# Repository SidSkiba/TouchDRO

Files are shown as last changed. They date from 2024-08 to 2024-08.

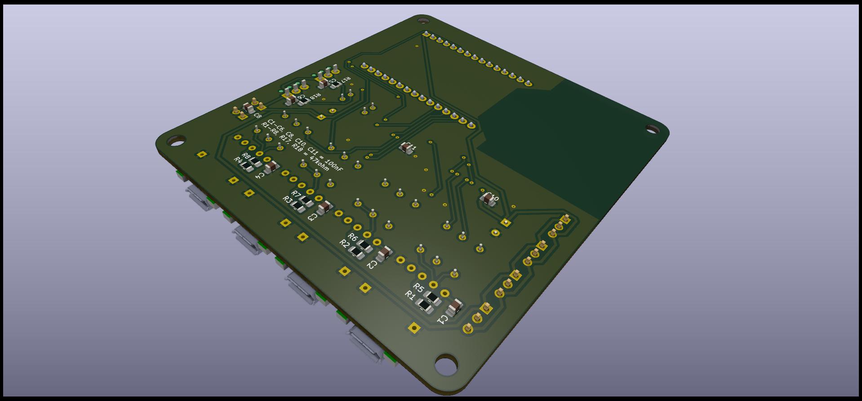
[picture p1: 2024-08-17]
Pictures/TouchDRO 6.jpg

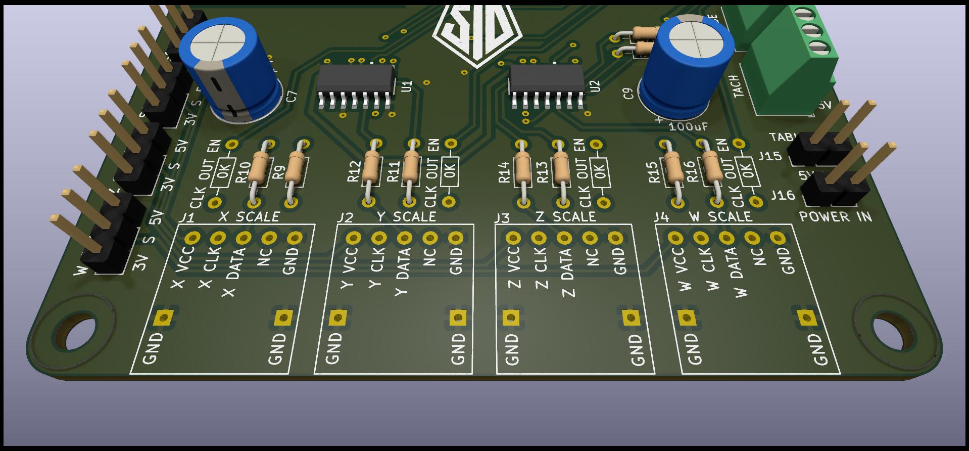
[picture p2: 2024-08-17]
Pictures/TouchDRO 10.jpg

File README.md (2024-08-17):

# TouchDRO
TocuhDRO PCB Kicad Design

PCB Design Files for a DIY TouchDRO PCB. This is based on information provided by https://www.touchdro.com/

All design done in Kicad 8.

Firmware files provided by https://www.touchdro.com/

All Gerber files included for JLCPCB to manufacture the circuit boards.

Design uses some surface mount components (some 0805 sized resistors and capacitors and sirface mount IC's) so you need to be comfortable with soldering those devices to the board.

Note that ESP32 module needs to be spaced 5mm above the circuit board.

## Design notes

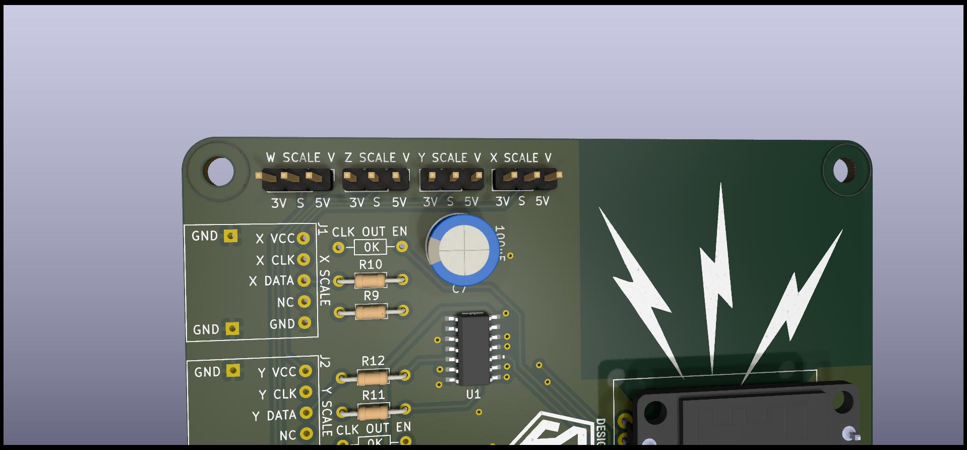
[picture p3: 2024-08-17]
Pictures/TouchDRO 11.jpg

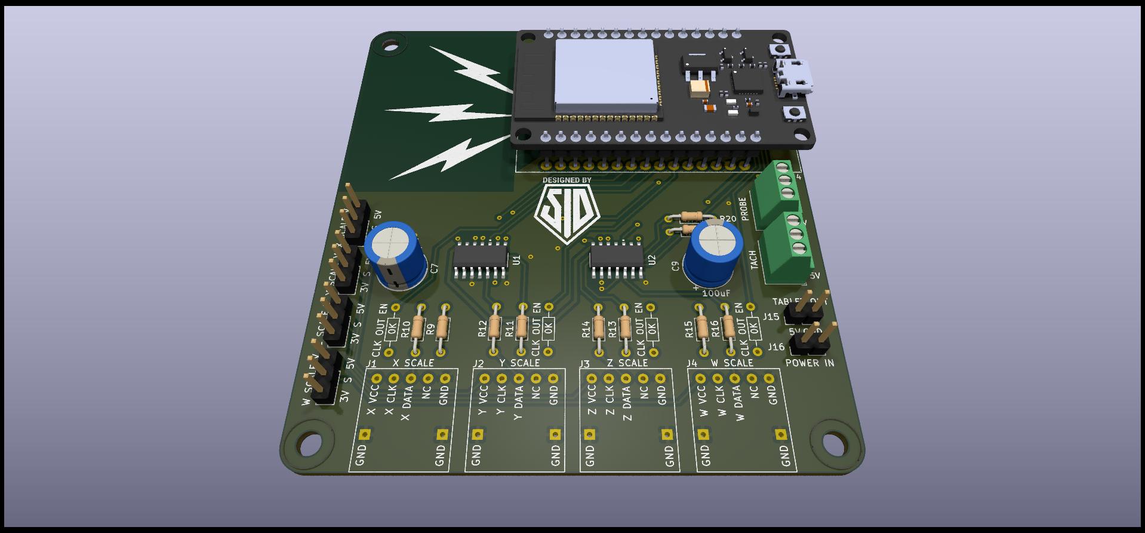
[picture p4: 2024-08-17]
Pictures/TouchDRO 9.jpg

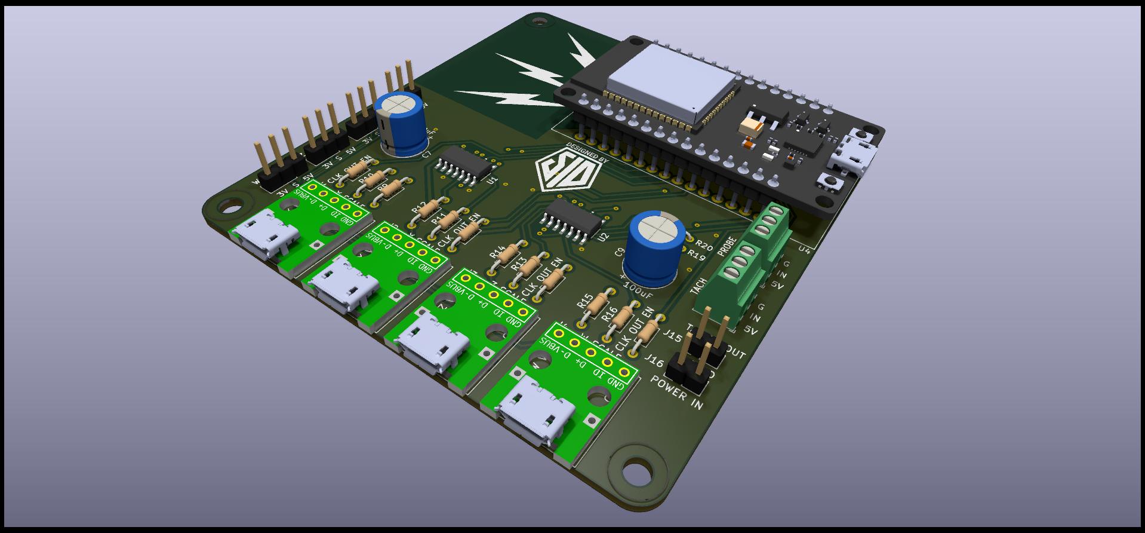
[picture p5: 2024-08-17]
Pictures/TouchDRO 4.jpg

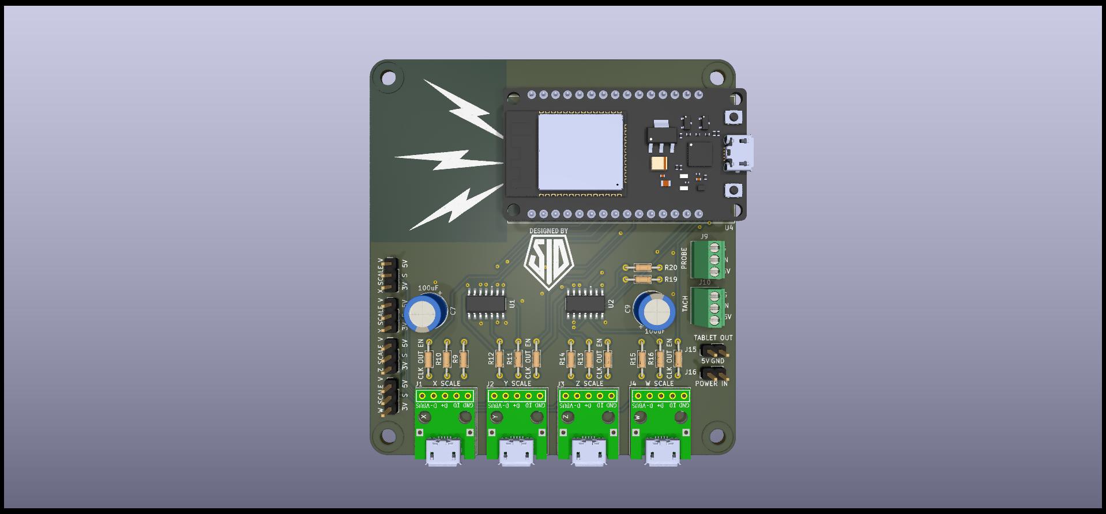
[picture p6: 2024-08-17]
Pictures/TouchDRO 2.jpg

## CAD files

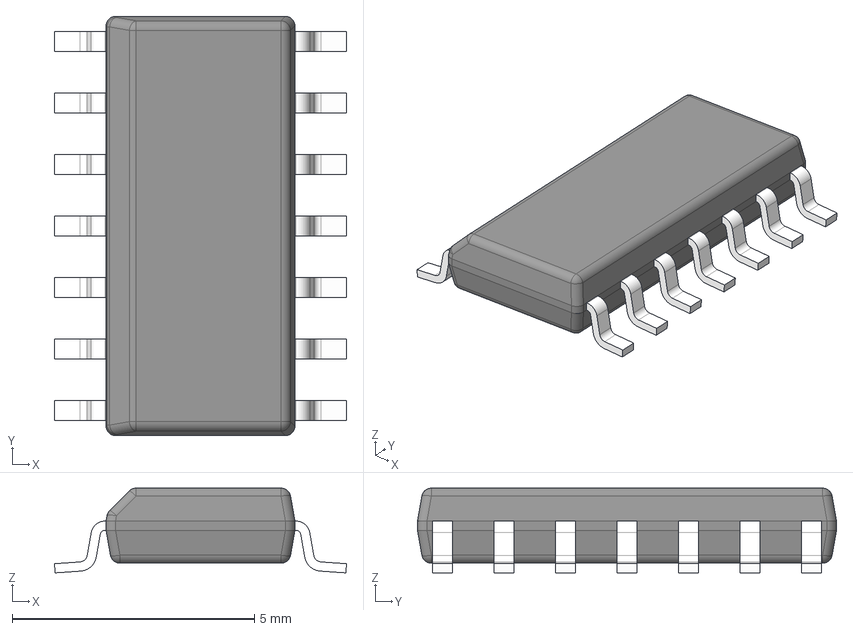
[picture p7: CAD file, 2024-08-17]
3D Models/CD74HC14M96.stp
6.03 x 8.65 x 1.75 mm
BODY-SO
LEAD-SO x 14
PIN1-ID

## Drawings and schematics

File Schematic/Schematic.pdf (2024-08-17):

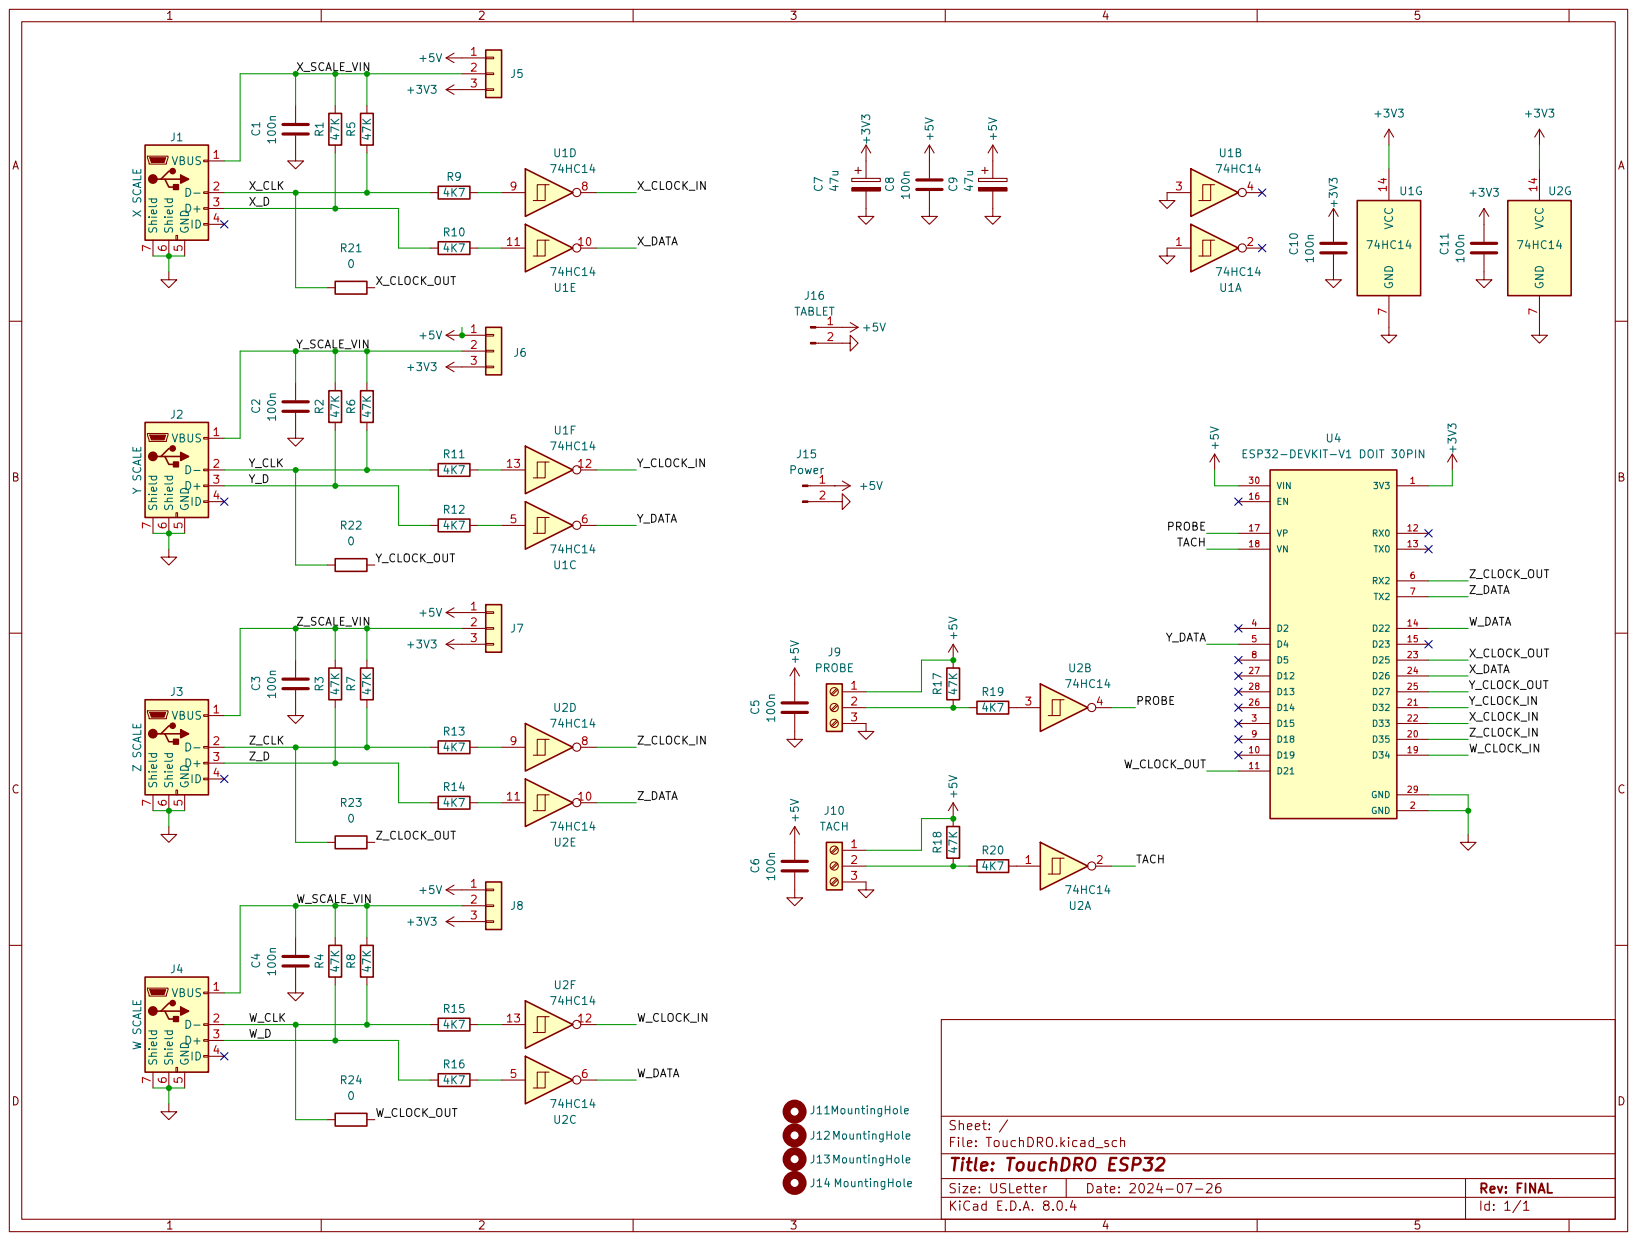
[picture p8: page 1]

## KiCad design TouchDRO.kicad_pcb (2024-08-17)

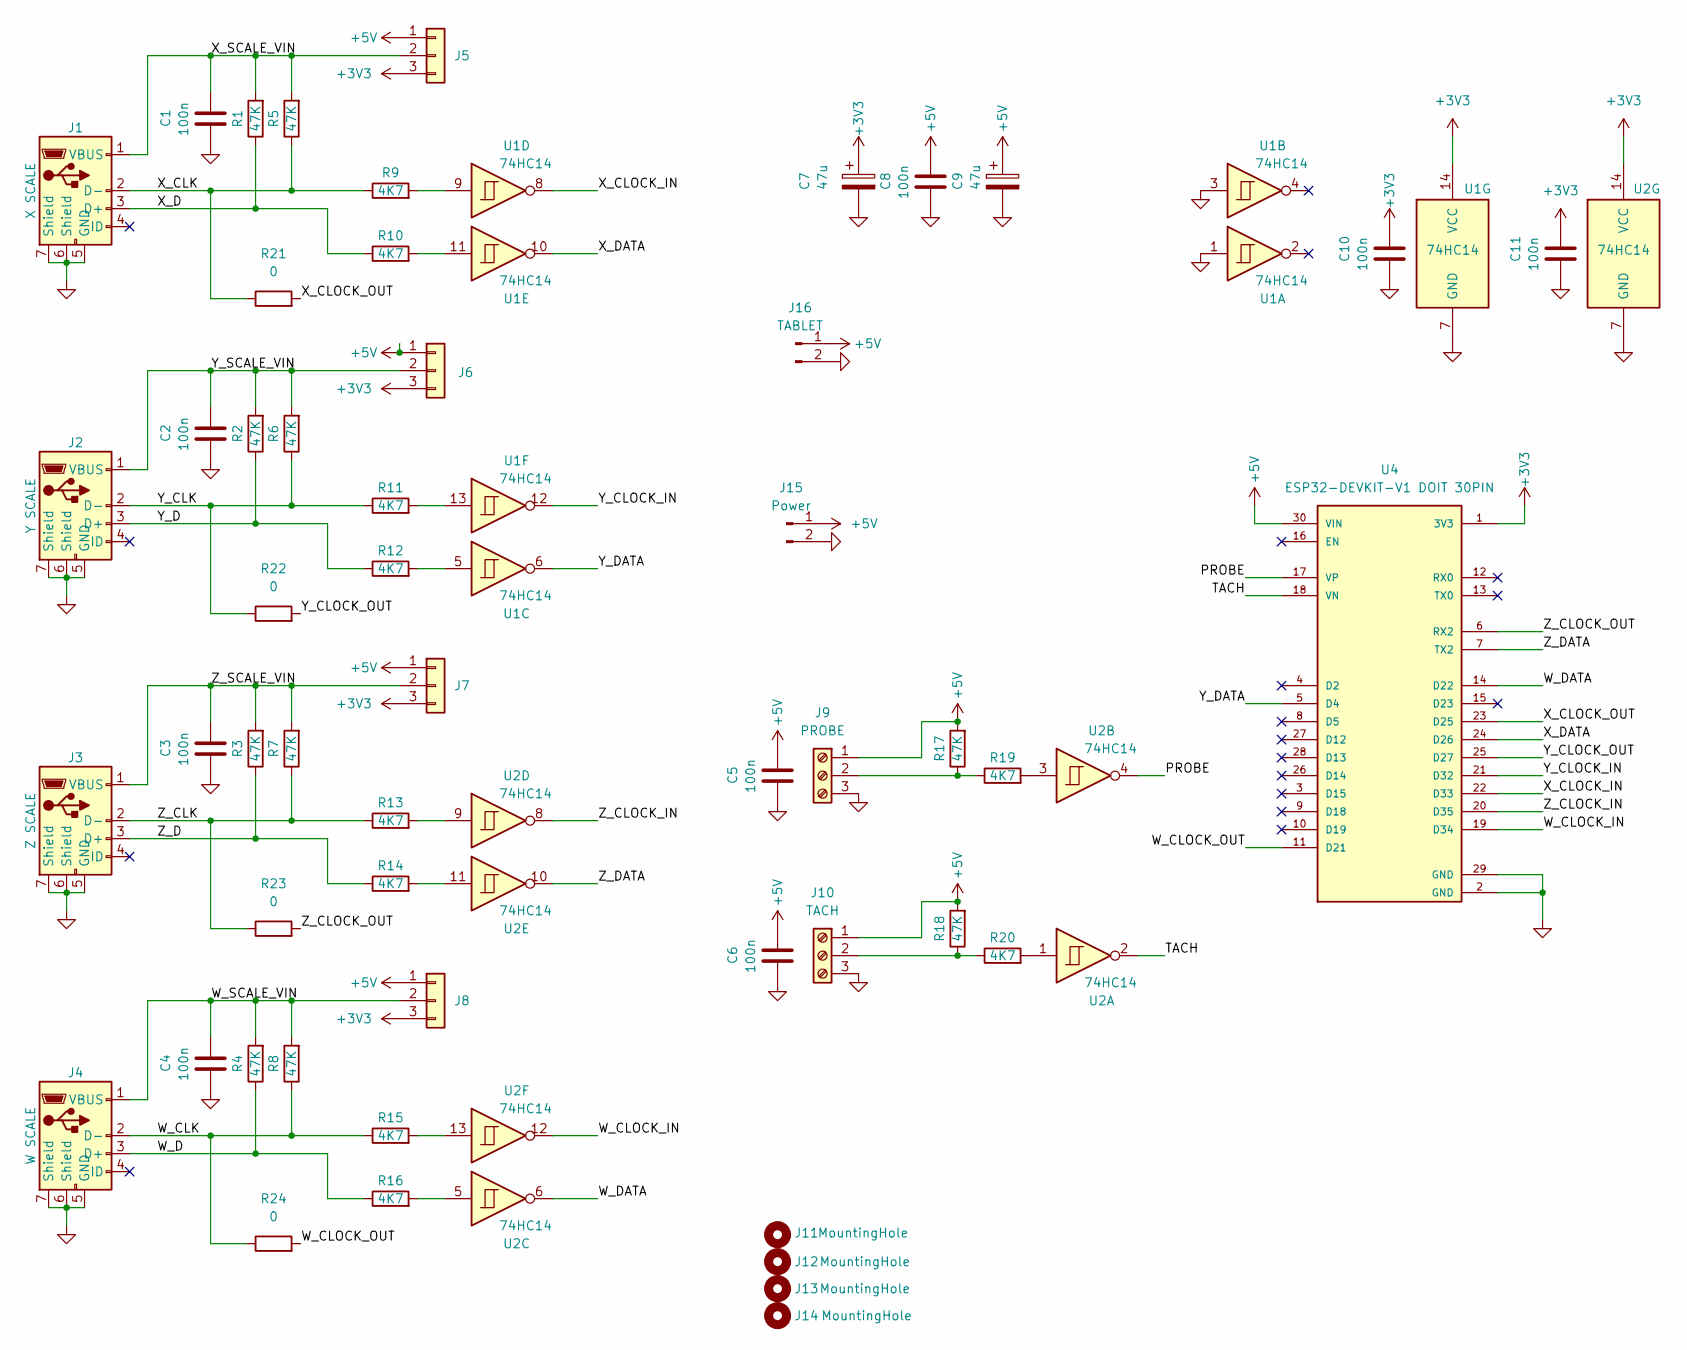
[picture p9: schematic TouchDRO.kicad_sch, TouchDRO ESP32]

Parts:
C1, C2, C3, C4, C5, C6, C8, C10, C11: 100n; C_0805_2012Metric_Pad1.18x1.45mm_HandSolder; LCSC C3034534
C7, C9: 47u; CP_Radial_D8.0mm_P3.50mm; LCSC 03EC0571
J1: X SCALE; USB Breakout Board
J2: Y SCALE; USB Breakout Board
J3: Z SCALE; USB Breakout Board
J4: W SCALE; USB Breakout Board
J5: X SCALE; PinHeader_1x03_P2.54mm_Vertical
J6: Y SCALE; PinHeader_1x03_P2.54mm_Vertical
J7: Z SCALE; PinHeader_1x03_P2.54mm_Vertical
J8: W SCALE; PinHeader_1x03_P2.54mm_Vertical
J9: PROBE; TerminalBlock_Phoenix_MPT-0,5-3-2.54_1x03_P2.54mm_Horizontal
J10: TACH; TerminalBlock_Phoenix_MPT-0,5-3-2.54_1x03_P2.54mm_Horizontal
J11, J12, J13, J14: MountingHole; MountingHole_3.5mm
J15: Power; PinHeader_1x02_P2.54mm_Vertical
J16: TABLET; PinHeader_1x02_P2.54mm_Vertical
R1, R2, R3, R4, R5, R6, R7, R8, R17, R18: 47K; R_0805_2012Metric_Pad1.20x1.40mm_HandSolder; LCSC C410613
R9, R10, R11, R12, R13, R14, R15, R16, R19, R20: 4K7; R_Axial_DIN0204_L3.6mm_D1.6mm_P7.62mm_Horizontal; LCSC C119339
R21, R22, R23, R24: 0; R_Axial_DIN0204_L3.6mm_D1.6mm_P7.62mm_Horizontal
U1, U2: 74HC14; 14PIN_SOIC; LCSC C2907
U4: ESP32-DEVKIT-V1 DOIT 30PIN; MODULE_ESP32_DEVKIT_V1 DOIT 30PIN; PARTREV N/A

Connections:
+3V3: C7.1, C10.1, C11.1, J5.3, J6.3, J7.3, J8.3, U1.14 (VCC), U2.14 (VCC), U4.1 (3V3)
+5V: C5.1, C6.1, C8.1, C9.1, J5.1, J6.1, J7.1, J8.1, J9.1, J10.1, J15.1, J16.1, R17.2, R18.2, U4.30 (VIN)
/PROBE: U2.4, U4.17 (VP)
/TACH: U2.2, U4.18 (VN)
/W_CLK: J4.2 (D-), R8.1, R15.1, R24.1
/W_CLOCK_IN: U2.12, U4.19 (D34)
/W_CLOCK_OUT: R24.2, U4.11 (D21)
/W_D: J4.3 (D+), R4.1, R16.1
/W_DATA: U2.6, U4.14 (D22)
/W_SCALE_VIN: C4.1, J4.1 (VBUS), J8.2, R4.2, R8.2
/X_CLK: J1.2 (D-), R5.1, R9.1, R21.1
/X_CLOCK_IN: U1.8, U4.22 (D33)
/X_CLOCK_OUT: R21.2, U4.23 (D25)
/X_D: J1.3 (D+), R1.1, R10.1
/X_DATA: U1.10, U4.24 (D26)
/X_SCALE_VIN: C1.1, J1.1 (VBUS), J5.2, R1.2, R5.2
/Y_CLK: J2.2 (D-), R6.1, R11.1, R22.1
/Y_CLOCK_IN: U1.12, U4.21 (D32)
/Y_CLOCK_OUT: R22.2, U4.25 (D27)
/Y_D: J2.3 (D+), R2.1, R12.1
/Y_DATA: U1.6, U4.5 (D4)
/Y_SCALE_VIN: C2.1, J2.1 (VBUS), J6.2, R2.2, R6.2
/Z_CLK: J3.2 (D-), R7.1, R13.1, R23.1
/Z_CLOCK_IN: U2.8, U4.20 (D35)
/Z_CLOCK_OUT: R23.2, U4.6 (RX2)
/Z_D: J3.3 (D+), R3.1, R14.1
/Z_DATA: U2.10, U4.7 (TX2)
/Z_SCALE_VIN: C3.1, J3.1 (VBUS), J7.2, R3.2, R7.2
GND: C1.2, C2.2, C3.2, C4.2, C5.2, C6.2, C7.2, C8.2, C9.2, C10.2, C11.2, J1.5 (GND), J1.6 (Shield), J1.7 (Shield), J2.5 (GND), J2.6 (Shield), J2.7 (Shield), J3.5 (GND), J3.6 (Shield), J3.7 (Shield), J4.5 (GND), J4.6 (Shield), J4.7 (Shield), J9.3, J10.3, J15.2, J16.2, U1.1, U1.3, U1.7 (GND), U2.7 (GND), U4.2 (GND), U4.29 (GND)
unnamed: J9.2, R17.1, R19.1
unnamed: J10.2, R18.1, R20.1
unnamed: R9.2, U1.9
unnamed: R10.2, U1.11
unnamed: R11.2, U1.13
unnamed: R12.2, U1.5
unnamed: R13.2, U2.9
unnamed: R14.2, U2.11
unnamed: R15.2, U2.13
unnamed: R16.2, U2.5
unnamed: R19.2, U2.3
unnamed: R20.2, U2.1

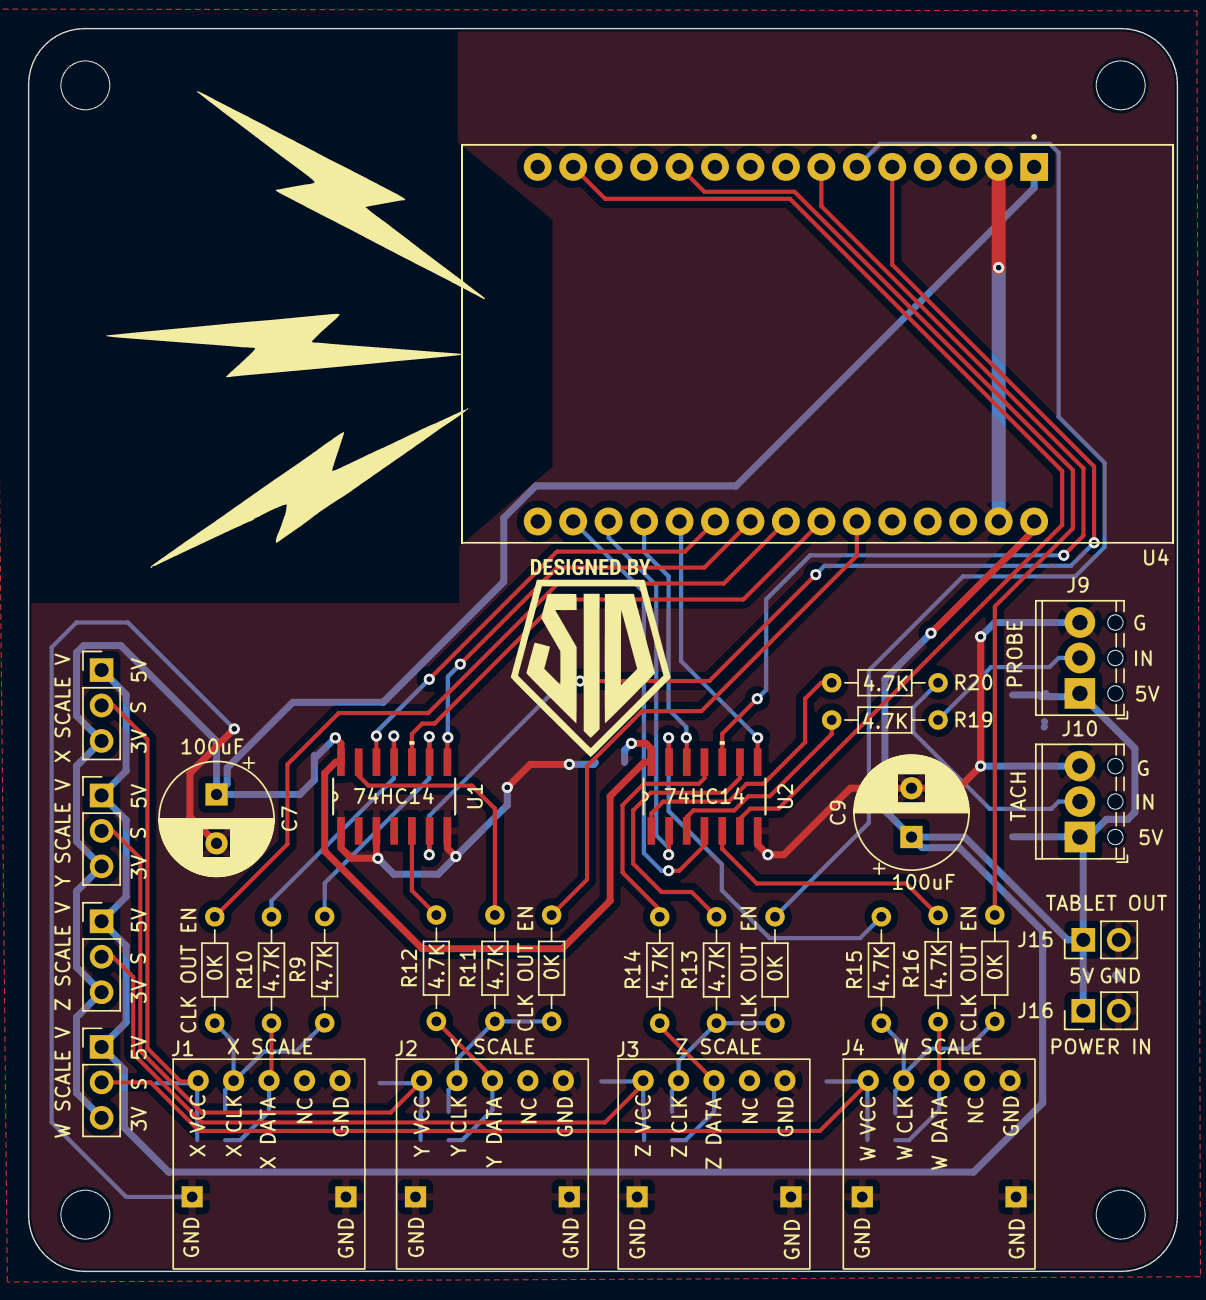
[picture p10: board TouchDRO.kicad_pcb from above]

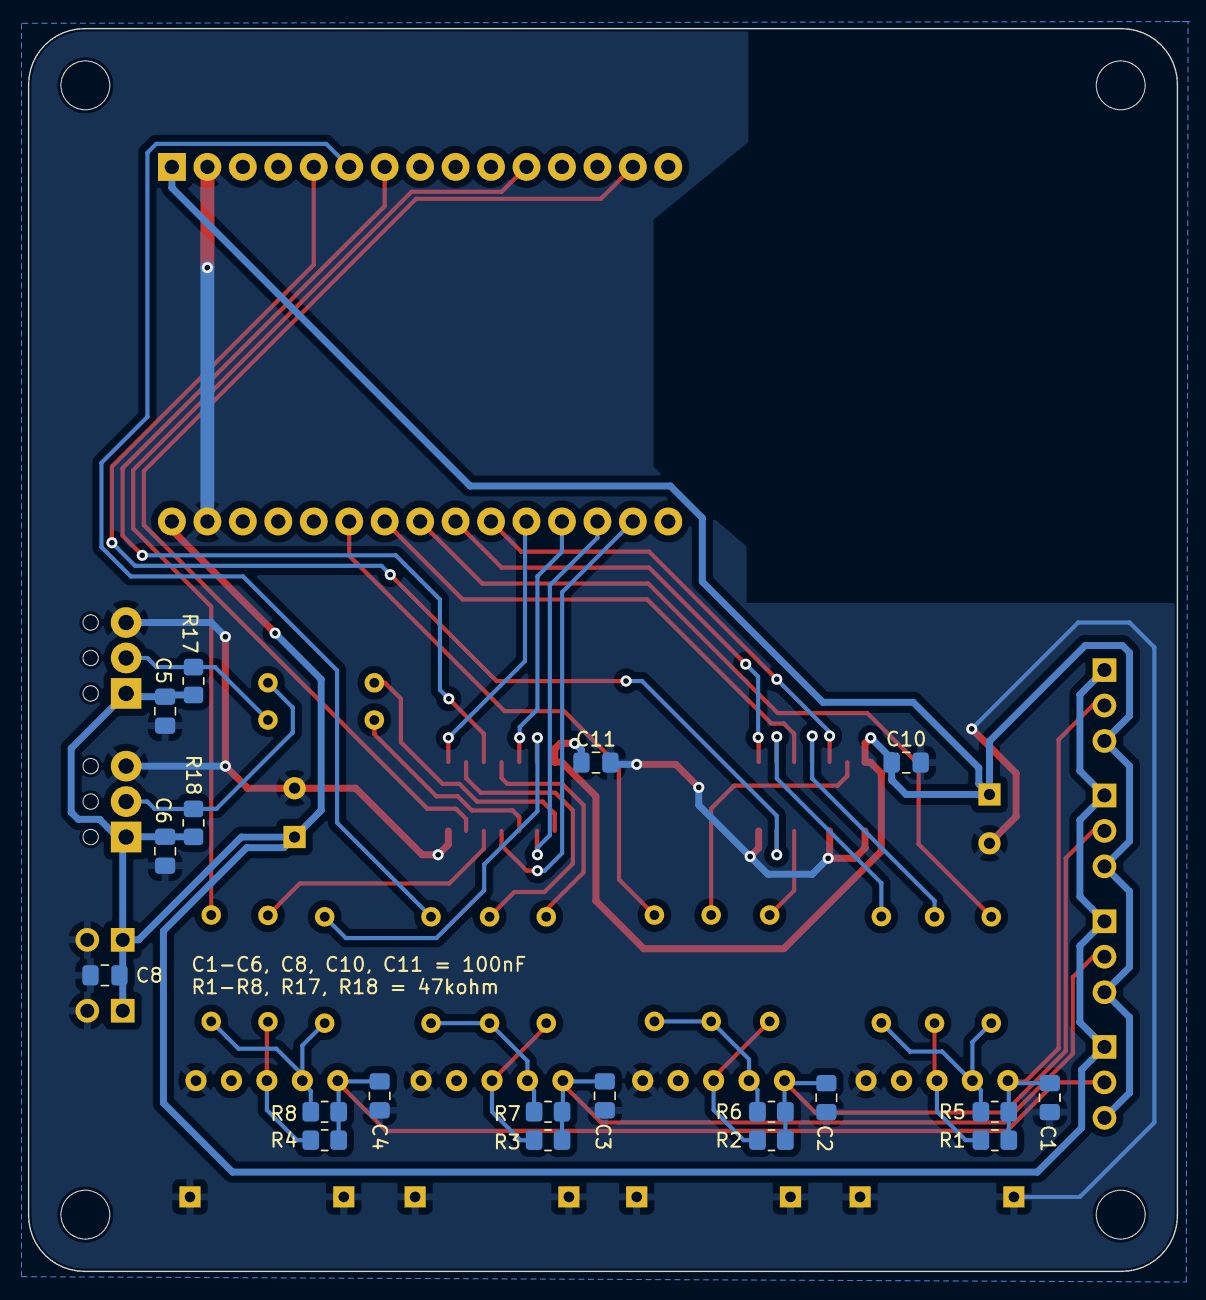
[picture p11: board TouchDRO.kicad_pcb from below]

Board: 2 copper layers, 82.3 x 89.0 mm, 54 parts (19 on the bottom side), 41 nets.
